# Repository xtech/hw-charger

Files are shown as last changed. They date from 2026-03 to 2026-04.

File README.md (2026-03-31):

# Universal OpenMower Charger

## Information

This hardware version is in beta state. Expect for things to not work at the current state!

## About This Repo

OpenMower is an open-source project that upgrades off-the-shelf robotic mowers into modern, smart lawn mowing robots with RTK GPS technology. For more details, check out the [OpenMower project](https://github.com/clemensElflein/openmower).

This repository contains the design files for a custom charger specifically designed for converting YardForce mowers to OpenMower. 

## Patents, Local Laws, Liability

Before building a robot based on the designs published here, please make sure that you are allowed to do so in your specific regions.
There may be patents and / or laws prohibiting you of doing so.

The code/schematics/PCB files are distributed in the hope that it will be useful, but WITHOUT ANY WARRANTY; without even the implied warranty of MERCHANTABILITY or FITNESS FOR A PARTICULAR PURPOSE.

This basically means: I'm just documenting a project of mine here for free and I don't have the time and resources to check that devices built using this information will be safe to use, legal to use or even work as intended. You will need technical know-how to use this project and I'm not liable for any damages your devices do to anyone or anything.

## License

<br />This work is licensed under a <a rel="license" href="https://creativecommons.org/licenses/by-nc/4.0/">Creative Commons Attribution-NonCommercial 4.0 International License</a>.

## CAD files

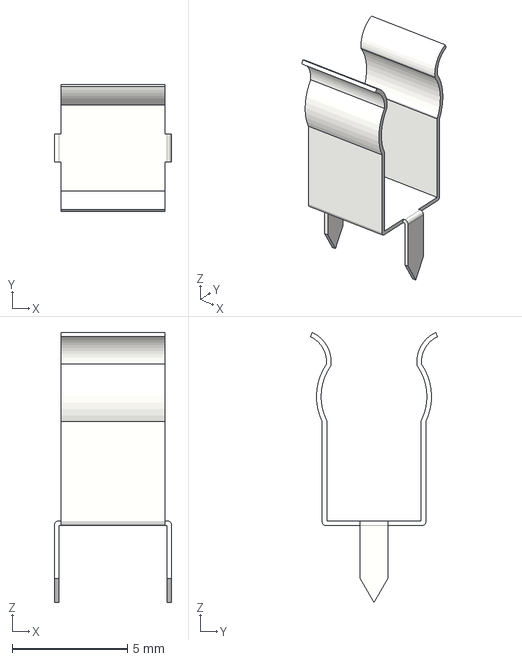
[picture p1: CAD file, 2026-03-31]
3d/FuseClip.stp
5.10 x 5.53 x 11.7 mm

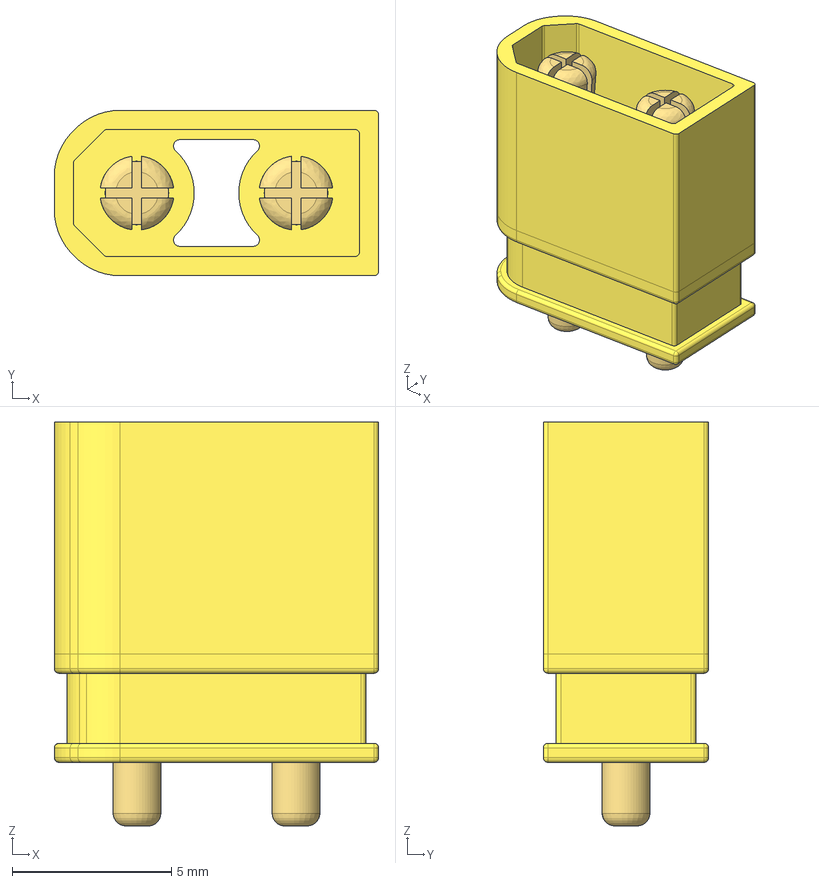
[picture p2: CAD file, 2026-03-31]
components/extern/3dmodels/easyeda2kicad/Amass_XT30UPB-M.step
10.2 x 5.20 x 12.7 mm

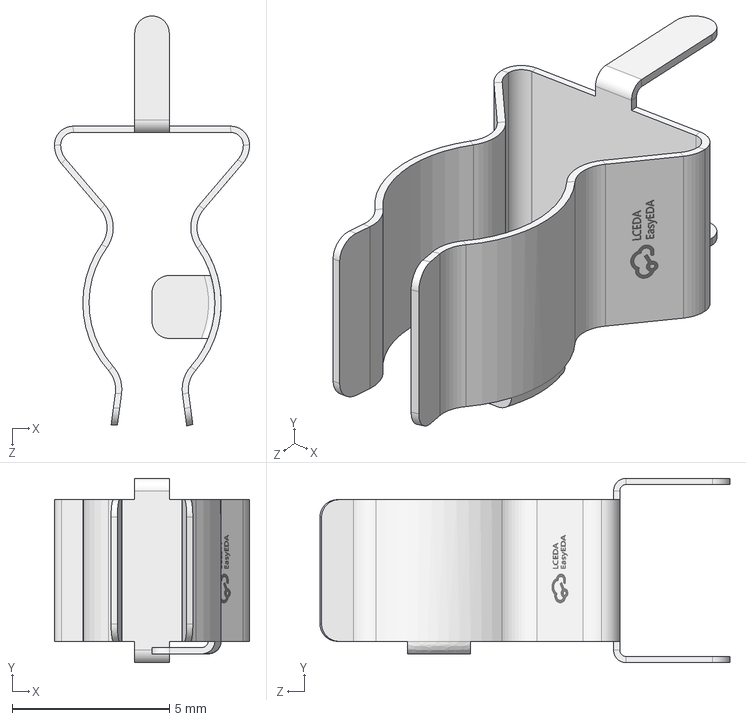
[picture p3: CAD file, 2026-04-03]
components/extern/3dmodels/local_FUSE/FUSE-TH_5X20.step
6.20 x 5.86 x 13.0 mm

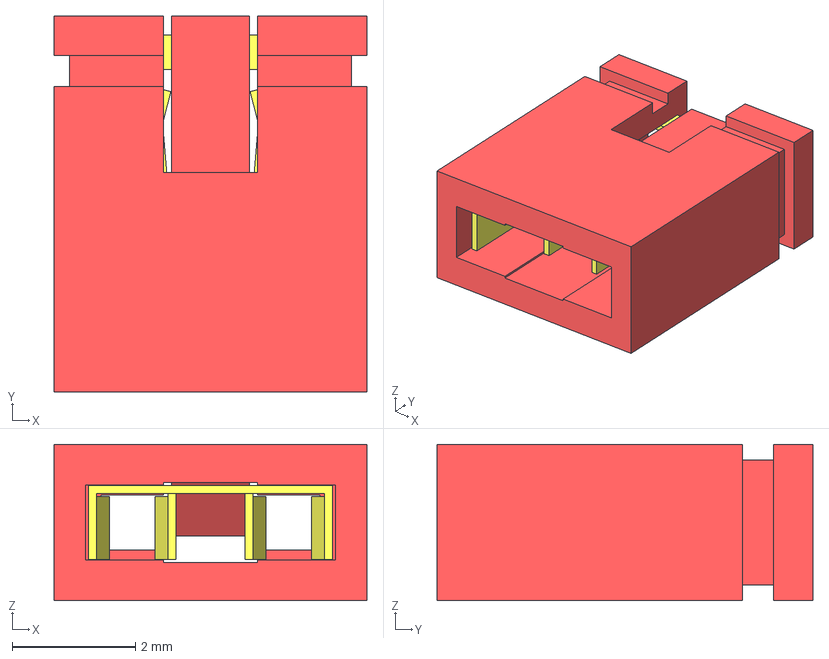
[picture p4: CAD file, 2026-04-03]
components/extern/3dmodels/SNT-100-RD-G.step
5.08 x 6.10 x 2.54 mm

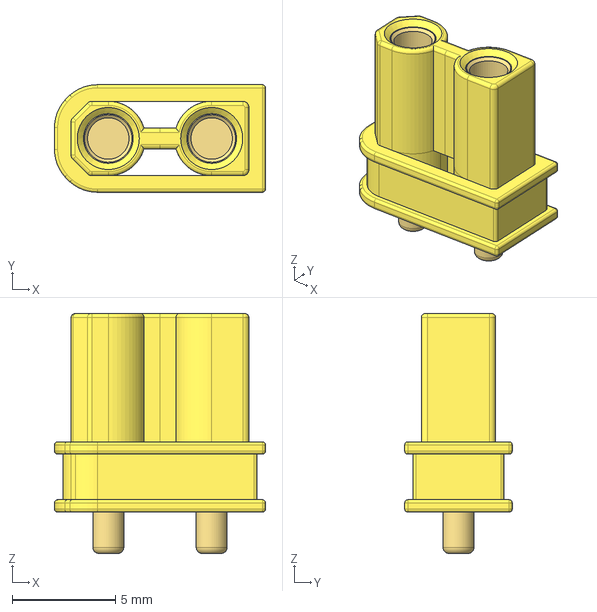
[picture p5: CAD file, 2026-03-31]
components/extern/3dmodels/easyeda2kicad/Amass_XT30UPB-F.step
10.2 x 5.20 x 11.6 mm

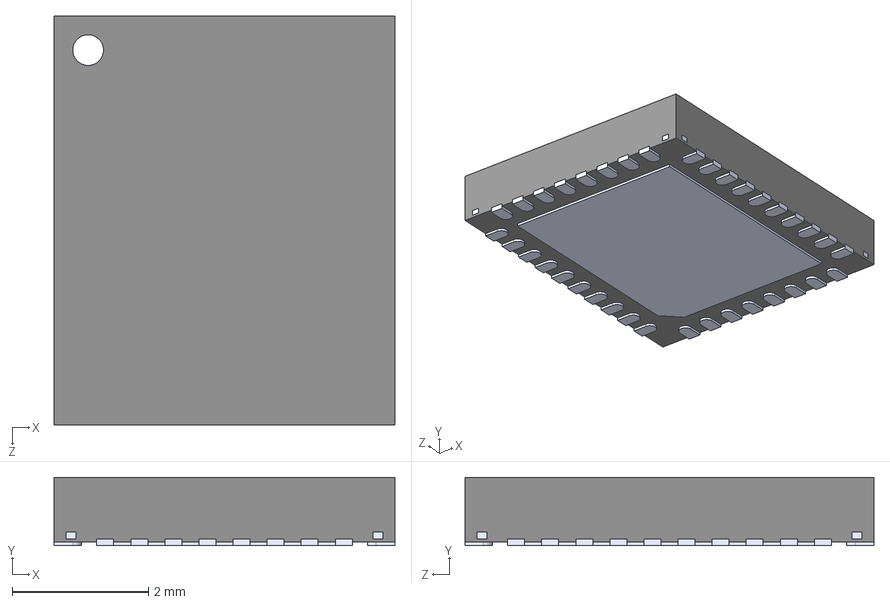
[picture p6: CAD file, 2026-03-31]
components/extern/3dmodels/local_CHARGER/BQ25756RRVR.step
5.00 x 1.00 x 6.00 mm

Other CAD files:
components/extern/3dmodels/SNT-100-BK-H.step
components/extern/3dmodels/SNT-100-BL-G.step

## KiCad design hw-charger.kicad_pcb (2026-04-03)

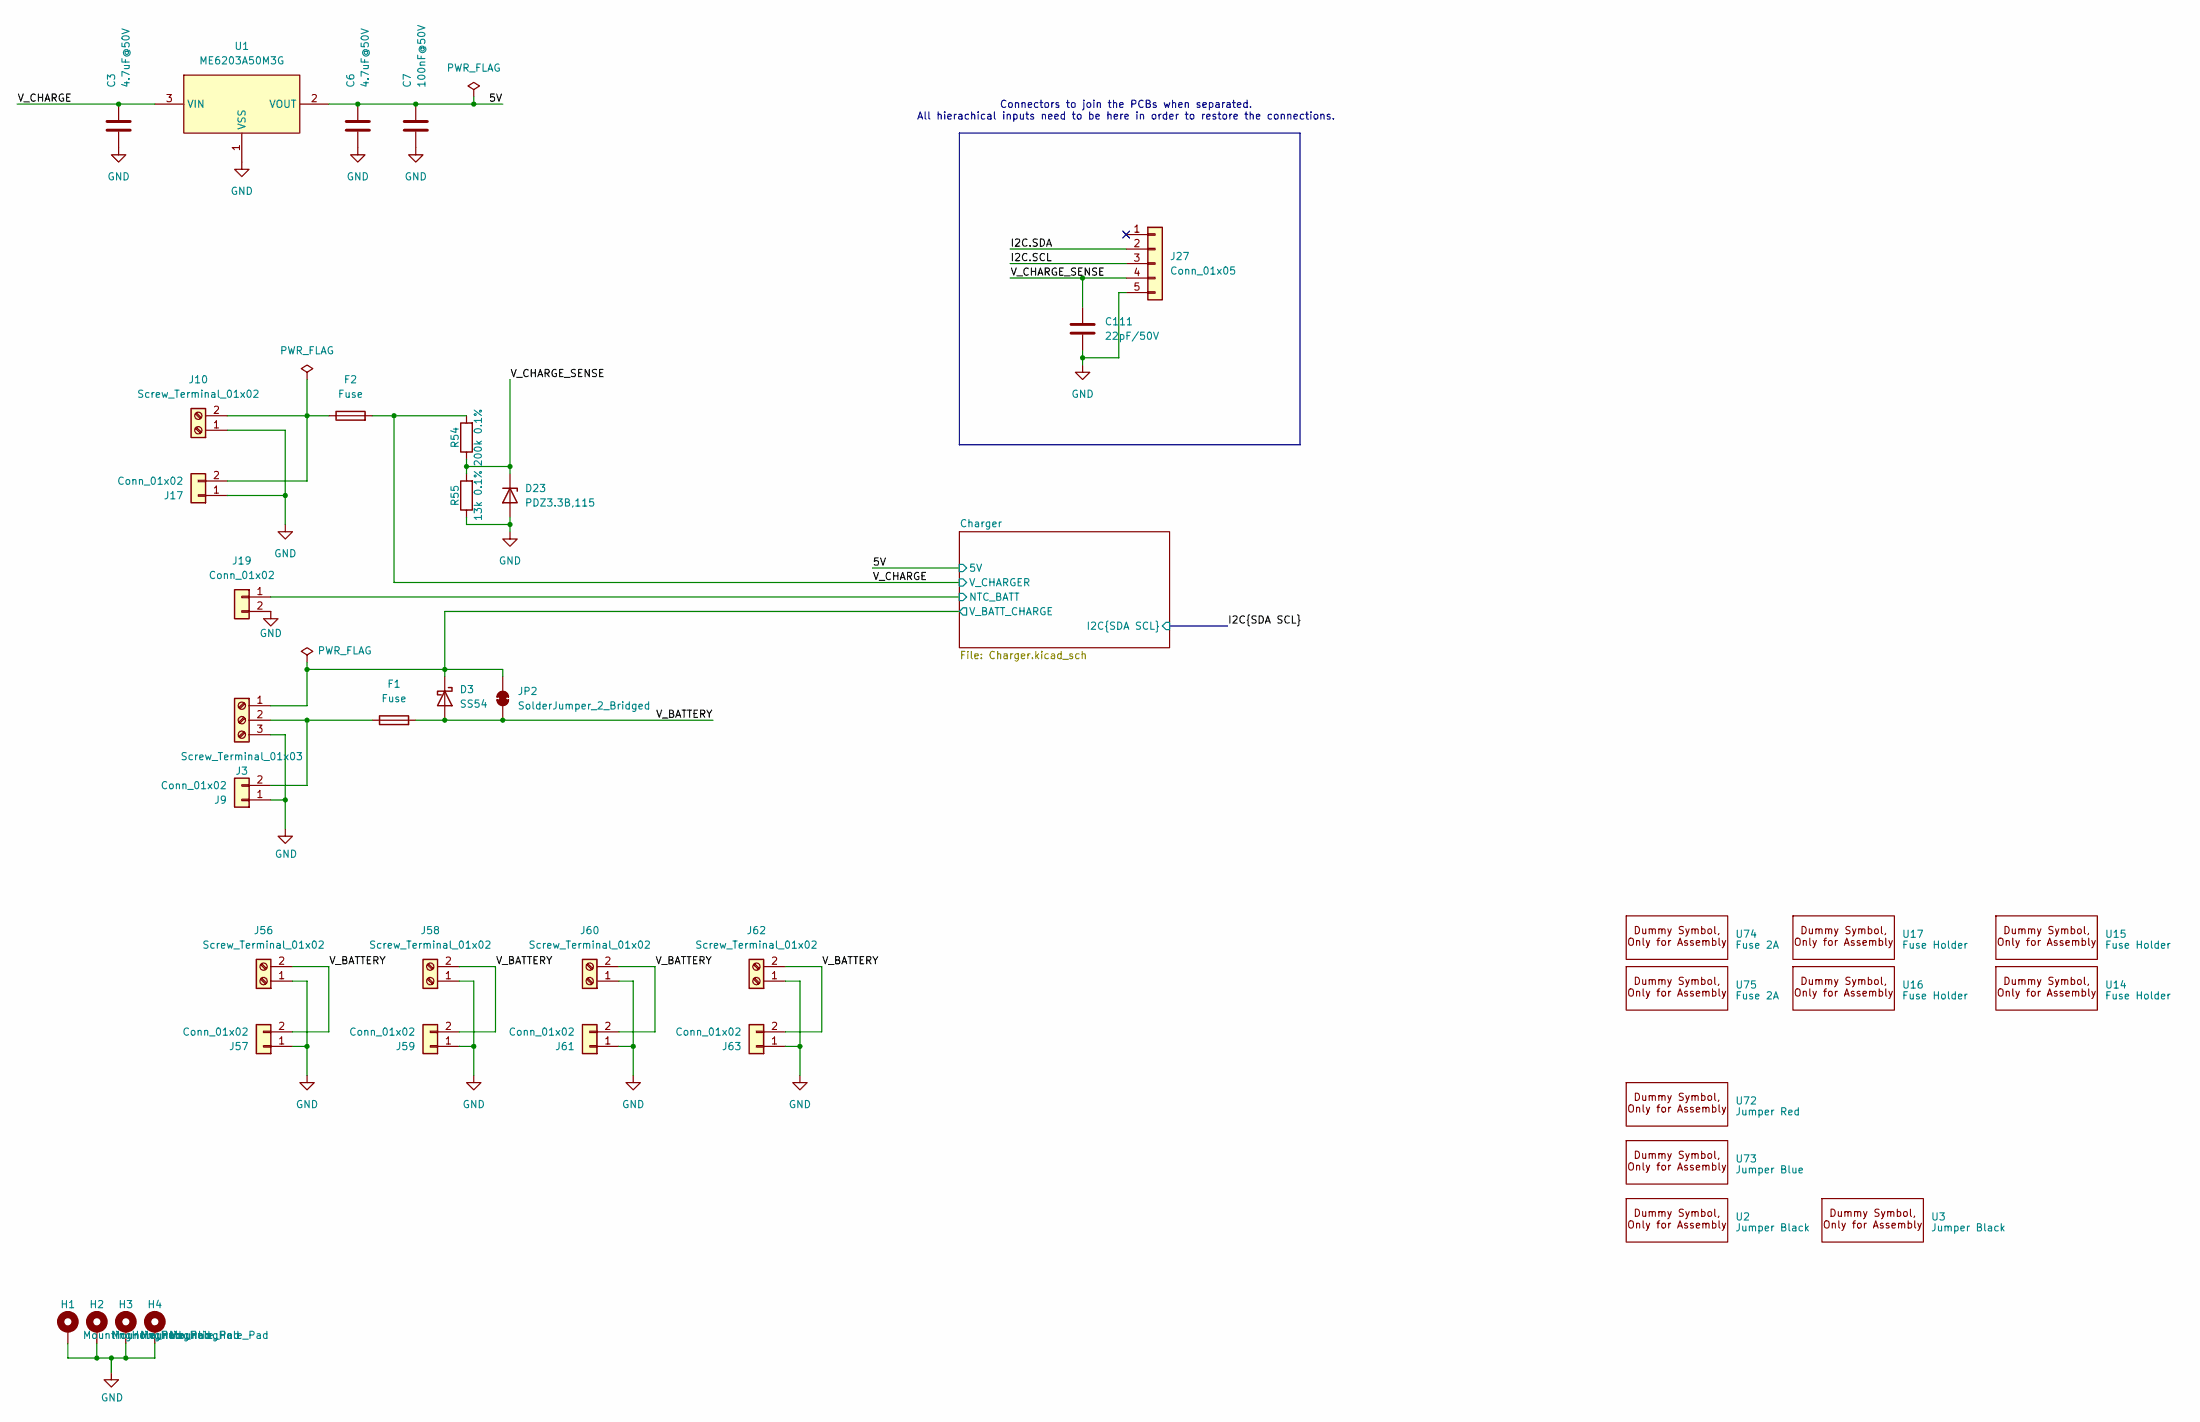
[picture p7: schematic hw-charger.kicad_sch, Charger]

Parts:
C3, C6: 4.7uF@50V; C_1206_3216Metric; JLC C29823
C7: 100nF@50V; C_0603_1608Metric; JLC C14663
C111: 22pF/50V; C_0603_1608Metric; JLC C1653
D3: SS54; D_SMA; Part Number SB54AFC_R1_00001; Digikey 3757-SB54AFC_R1_00001CT-ND
D23: PDZ3.3B,115; D_SOD-323; JLC C426855
F1, F2: Fuse; Fuseholder5x20_horiz_open_inline_C3130; JLC C3130
H1, H2, H3, H4: MountingHole_Pad; MountingHole_4.3mm_M4_Pad_Via
J3: Screw_Terminal_01x03; TerminalBlock_Phoenix_MKDS-1,5-3-5.08_1x03_P5.08mm_Horizont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; JLC C557666
J9, J17: Conn_01x02; AMASS_XT30U-M_1x02_P5.0mm_Vertical_mod; JLC C99101
J10, J56, J58, J60, J62: Screw_Terminal_01x02; TerminalBlock_Phoenix_MKDS-1,5-2-5.08_1x02_P5.08mm_Horizont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; JLC C557665
J19: Conn_01x02; JST_XH_B2B-XH-A_1x02_P2.50mm_Vertical; JLC C2910525
J27: Conn_01x05; JST_XH_B5B-XH-A_1x05_P2.50mm_Vertical; JLC C157991
J57, J59, J61, J63: Conn_01x02; AMASS_XT30U-F_1x02_P5.0mm_Vertical_mod; JLC C99102
JP2: SolderJumper_2_Bridged; SolderJumper-2_P1.3mm_Bridged2Bar_Pad1.0x1.5mm
R54: 200k 0.1%; R_0402_1005Metric; JLC C728556
R55: 13k 0.1%; R_0402_1005Metric; JLC C852524
U1: ME6203A50M3G; SOT-23-3_L2.9-W1.6-P1.90-LS2.8-BR; LCSC Part C92717
U2, U3: Jumper Black; SNT-100-BK-H; JLC C100114
U14, U15, U16, U17: Fuse Holder; Dummy; JLC C3130
U72: Jumper Red; SNT-100-RD-G; JLC C20417889
U73: Jumper Blue; SNT-100-BL-H; JLC C20417886
U74, U75: Fuse 2A; Dummy; JLC C356459

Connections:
/5V: C6.1, C7.2, U1.2 (VOUT); also elsewhere on the board
/Charger/NTC_BATT: J19.1; also elsewhere on the board
/Charger/V_BATT_CHARGE: D3.1 (K), J3.1, JP2.2 (B); also elsewhere on the board
/I2C.SCL: J27.3; also elsewhere on the board
/I2C.SDA: J27.2; also elsewhere on the board
/V_BATTERY: D3.2 (A), F1.2, J56.2, J57.2, J58.2, J59.2, J60.2, J61.2, J62.2, J63.2, JP2.1 (A)
/V_CHARGE: C3.1, F2.2, R54.2, U1.3 (VIN); also elsewhere on the board
/V_CHARGE_SENSE: C111.1, D23.1 (K), J27.4, R54.1, R55.2
GND: C3.2, C6.2, C7.1, C111.2, D23.2 (A), H1.1, H2.1, H3.1, H4.1, J3.3, J9.1, J10.1, J17.1, J19.2, J27.5, J56.1, J57.1, J58.1, J59.1, J60.1, J61.1, J62.1, J63.1, R55.1, U1.1 (VSS); also elsewhere on the board
unnamed: F1.1, J3.2, J9.2
unnamed: F2.1, J10.2, J17.2

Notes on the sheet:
Connectors to join the PCBs when separated. All hierachical inputs need to be here in order to restore the connections.

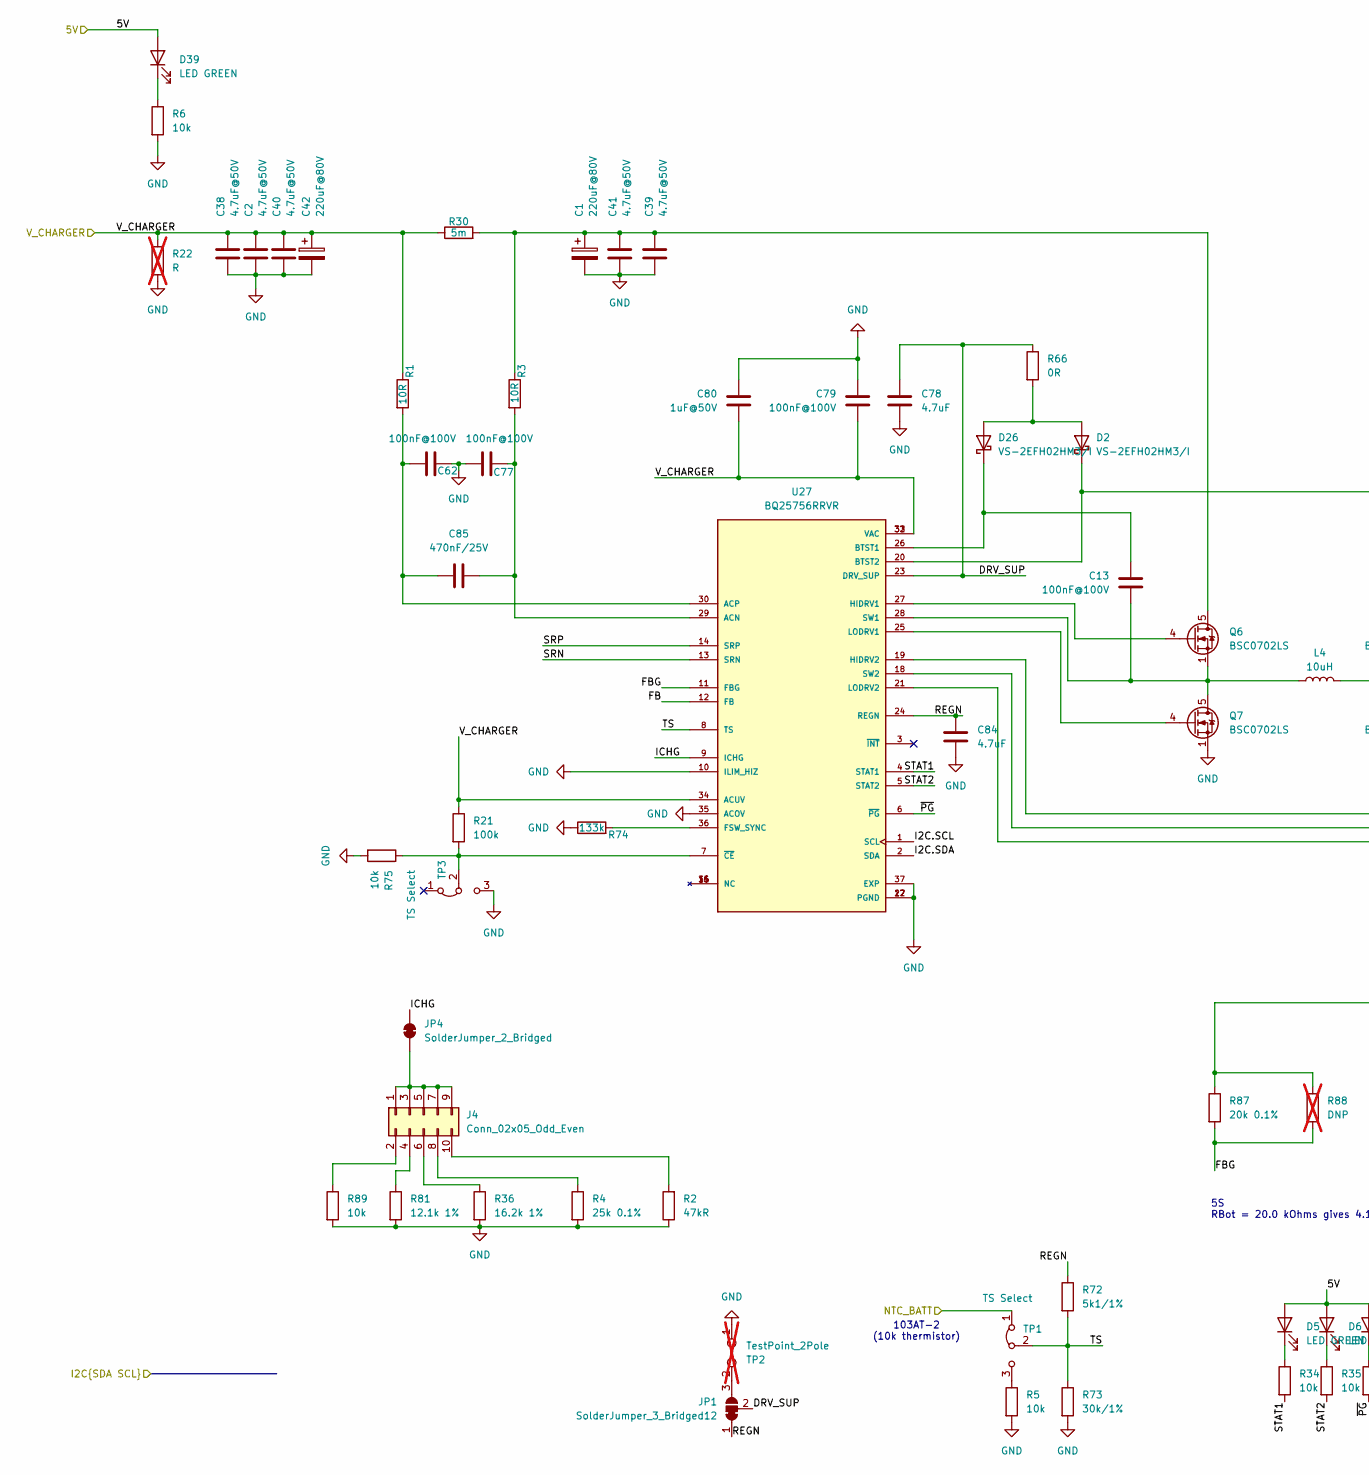
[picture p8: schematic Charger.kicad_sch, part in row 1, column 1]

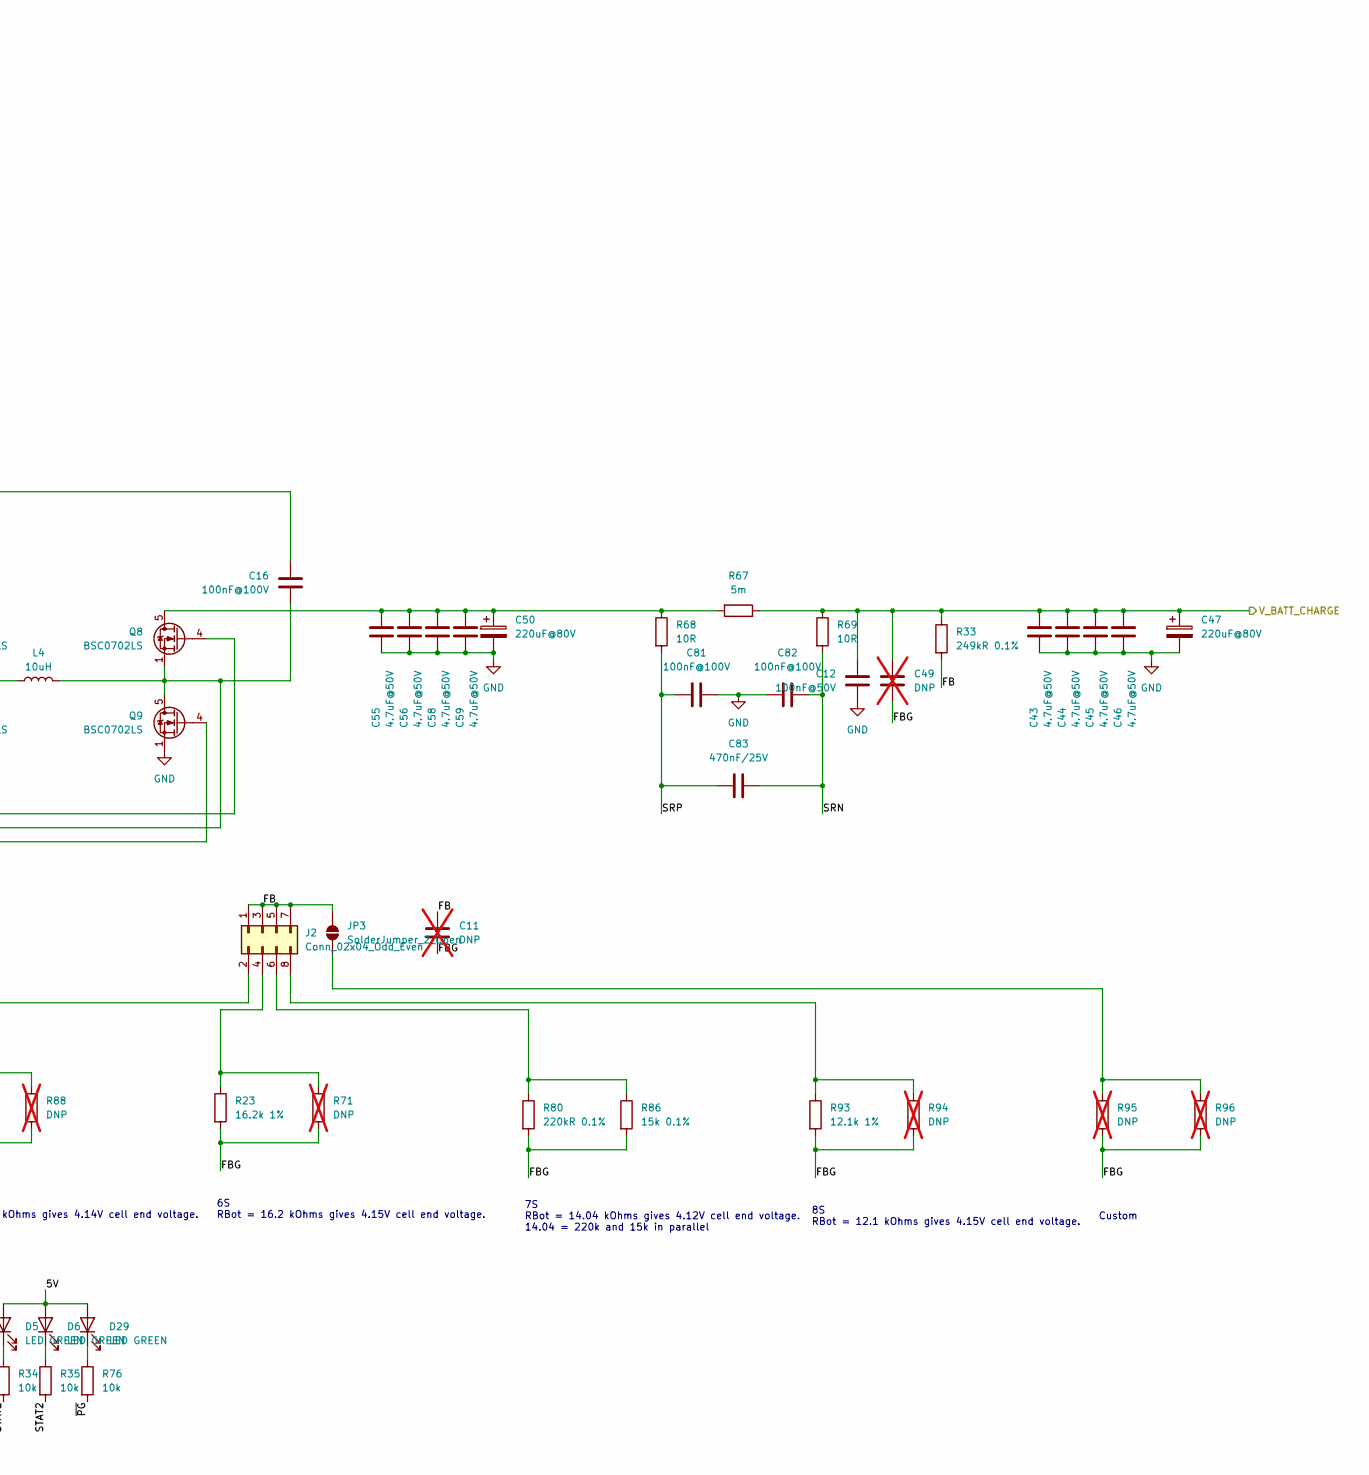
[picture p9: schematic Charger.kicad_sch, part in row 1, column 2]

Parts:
C1, C42, C47, C50: 220uF@80V; CP_Radial_D10.0mm_P5.00mm; JLC C2937593
C2, C38, C39, C40, C41, C43, C44, C45, C46, C55, C56, C58, C59: 4.7uF@50V; C_1206_3216Metric; JLC C29823
C11, C49: DNP; C_0603_1608Metric; not fitted
C12: 100nF@50V; C_0603_1608Metric; JLC C14663
C13, C16, C62, C77, C79, C81, C82: 100nF@100V; C_0805_2012Metric; JLC C28233
C78, C84: 4.7uF; C_0805_2012Metric; JLC C1779
C80: 1uF@50V; C_0805_2012Metric; JLC C28323
C83, C85: 470nF/25V; C_0603_1608Metric; JLC C1623
D2, D26: VS-2EFH02HM3/I; D_SMF; JLC C241868
D5, D6, D29, D39: LED GREEN; LED_0805_2012Metric; JLC C2297
J2: Conn_02x04_Odd_Even; PinHeader_2x04_P2.54mm_Vertical; JLC C5383105
J4: Conn_02x05_Odd_Even; PinHeader_2x05_P2.54mm_Vertical; JLC C706895
JP1: SolderJumper_3_Bridged12; SolderJumper-3_P1.3mm_Bridged12_Pad1.0x1.5mm
JP3: SolderJumper_2_Open; SolderJumper-2_P1.3mm_Open_Pad1.0x1.5mm
JP4: SolderJumper_2_Bridged; SolderJumper-2_P1.3mm_Bridged_Pad1.0x1.5mm
L4: 10uH; L_Sunlord_MWSA1004S; JLC C408487
Q6, Q7, Q8, Q9: BSC0702LS; TDSON-8-1; JLC C501503
R1, R3, R68, R69: 10R; R_0603_1608Metric; JLC C22859
R2: 47kR; R_0603_1608Metric; JLC C25819
R4: 25k 0.1%; R_0603_1608Metric; JLC C2828637
R5, R6, R34, R35, R75, R76: 10k; R_0402_1005Metric; JLC C25744
R21: 100k; R_0402_1005Metric; JLC C25741
R22: R; R_1206_3216Metric; not fitted
R23, R36: 16.2k 1%; R_0603_1608Metric; JLC C22885
R30, R67: 5m; R_2512_6332Metric; JLC C185817
R33: 249kR 0.1%; R_0603_1608Metric; JLC C705752
R66: 0R; R_0805_2012Metric; JLC C17477
R71, R88, R94, R95, R96: DNP; R_0603_1608Metric; not fitted
R72: 5k1/1%; R_0603_1608Metric; JLC C23186
R73: 30k/1%; R_0603_1608Metric; JLC C22984
R74: 133k; R_0603_1608Metric; JLC C227577
R80: 220kR 0.1%; R_0603_1608Metric; JLC C278545
R81, R93: 12.1k 1%; R_0603_1608Metric; JLC C22864
R86: 15k 0.1%; R_0603_1608Metric; JLC C2692707
R87: 20k 0.1%; R_0603_1608Metric; JLC C4184
R89: 10k; R_0603_1608Metric; JLC C25804
TP1, TP3: TS Select; PinHeader_1x03_P2.54mm_Vertical; JLC C49257
TP2: TestPoint_2Pole; PinHeader_1x02_P2.54mm_Vertical; not fitted
U27: BQ25756RRVR; PARTREV August 2023; JLC C19272232

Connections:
/5V: D5.2 (A), D6.2 (A), D29.2 (A), D39.2 (A); also elsewhere on the board
/Charger/DRV_SUP: C78.1, JP1.2 (C), R66.1, U27.23 (DRV_SUP)
/Charger/FB: C11.1, J2.1, J2.3, J2.5, J2.7, JP3.2 (B), R33.2, U27.12 (FB)
/Charger/FBG: C11.2, C49.2, R23.2, R71.2, R80.2, R86.2, R87.2, R88.2, R93.2, R94.2, R95.2, R96.2, U27.11 (FBG)
/Charger/ICHG: JP4.2 (B), U27.9 (ICHG)
/Charger/NTC_BATT: TP1.1 (A); also elsewhere on the board
/Charger/REGN: C84.1, JP1.1 (A), R72.1, U27.24 (REGN)
/Charger/SRN: C82.1, C83.2, R69.2, U27.13 (SRN)
/Charger/SRP: C81.2, C83.1, R68.2, U27.14 (SRP)
/Charger/STAT1: R34.2, U27.4 (STAT1)
/Charger/STAT2: R35.2, U27.5 (STAT2)
/Charger/TS: R72.2, R73.1, TP1.2 (C), U27.8 (TS)
/Charger/V_BATT_CHARGE: C12.2, C43.1, C44.1, C45.1, C46.1, C47.1, C49.1, R33.1, R67.1, R69.1; also elsewhere on the board
/Charger/~PG: R76.2, U27.6 (~PG)
/I2C.SCL: U27.1 (SCL); also elsewhere on the board
/I2C.SDA: U27.2 (SDA); also elsewhere on the board
/V_CHARGE: C2.1, C38.1, C40.1, C42.1, C79.1, C80.1, R1.1, R21.1, R22.1, R30.1, U27.32 (VAC), U27.33 (VAC), U27.34 (ACUV); also elsewhere on the board
GND: C1.2, C2.2, C12.1, C38.2, C39.2, C40.2, C41.2, C42.2, C43.2, C44.2, C45.2, C46.2, C47.2, C50.2, C55.2, C56.2, C58.2, C59.2, C62.2, C77.1, C78.2, C79.2, C80.2, C81.1, C82.2, C84.2, Q7.1 (S), Q7.2 (S), Q7.3 (S), Q9.1 (S), Q9.2 (S), Q9.3 (S), R2.1, R4.2, R5.2, R6.2, R22.2, R36.2, R73.2, R74.1, R75.2, R81.2, R89.2, TP2.1, TP3.3 (B), U27.10 (ILIM_HIZ), U27.17 (PGND), U27.22 (PGND), U27.35 (ACOV), U27.37 (EXP); also elsewhere on the board
unnamed: D2.2 (A), D26.2 (A), R66.2
unnamed: C16.2, D2.1 (K), U27.20 (BTST2)
unnamed: D5.1 (K), R34.1
unnamed: D6.1 (K), R35.1
unnamed: C13.2, D26.1 (K), U27.26 (BTST1)
unnamed: D29.1 (K), R76.1
unnamed: D39.1 (K), R6.1
unnamed: J2.2, R87.1, R88.1
unnamed: J2.4, R23.1, R71.1
unnamed: J2.6, R80.1, R86.1
unnamed: J2.8, R93.1, R94.1
unnamed: J4.1, J4.3, J4.5, J4.7, J4.9, JP4.1 (A)
unnamed: J4.2, R89.1
unnamed: J4.4, R81.1
unnamed: J4.6, R36.1
unnamed: J4.8, R4.1
unnamed: J4.10, R2.2
unnamed: JP1.3 (B), TP2.2
unnamed: JP3.1 (A), R95.1, R96.1
unnamed: C1.1, C39.1, C41.1, Q6.5 (D), R3.1, R30.2
unnamed: Q6.4 (G), U27.27 (HIDRV1)
unnamed: C13.1, L4.1, Q6.1 (S), Q6.2 (S), Q6.3 (S), Q7.5 (D), U27.28 (SW1)
unnamed: Q7.4 (G), U27.25 (LODRV1)
unnamed: C50.1, C55.1, C56.1, C58.1, C59.1, Q8.5 (D), R67.2, R68.1
unnamed: Q8.4 (G), U27.19 (HIDRV2)
unnamed: C16.1, L4.2, Q8.1 (S), Q8.2 (S), Q8.3 (S), Q9.5 (D), U27.18 (SW2)
unnamed: Q9.4 (G), U27.21 (LODRV2)
unnamed: R5.1, TP1.3 (B)
unnamed: R21.2, R75.1, TP3.2 (C), U27.7 (~CE)
unnamed: C77.2, C85.1, R3.2, U27.29 (ACN)
unnamed: C62.1, C85.2, R1.2, U27.30 (ACP)
unnamed: R74.2, U27.36 (FSW_SYNC)

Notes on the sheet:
6S RBot = 16.2 kOhms gives 4.15V cell end voltage.
103AT-2 (10k thermistor)
Custom
7S RBot = 14.04 kOhms gives 4.12V cell end voltage. 14.04 = 220k and 15k in parallel
5S RBot = 20.0 kOhms gives 4.14V cell end voltage.
8S RBot = 12.1 kOhms gives 4.15V cell end voltage.

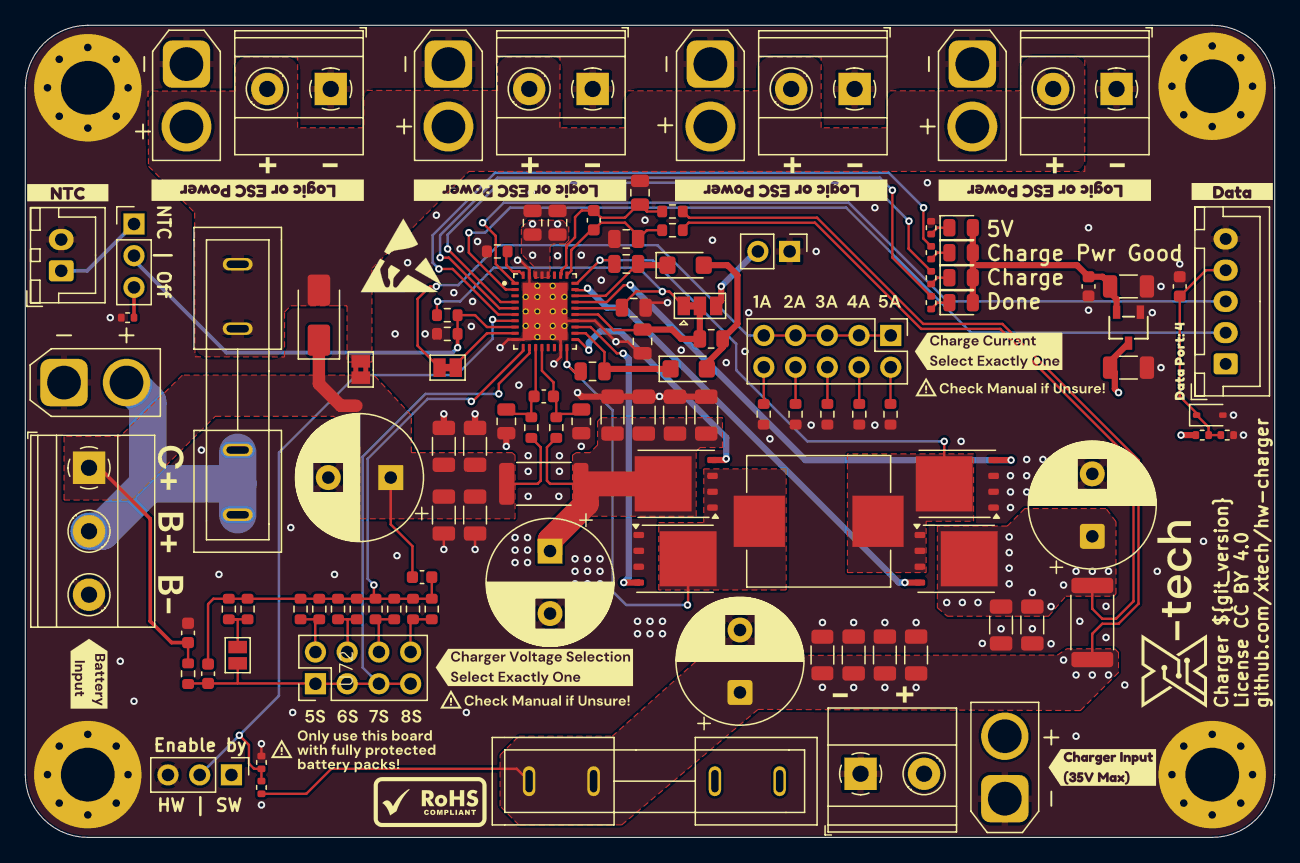
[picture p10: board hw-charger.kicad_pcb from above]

Board: 4 copper layers, 100.0 x 65.0 mm, 163 parts (0 on the bottom side), 54 nets.

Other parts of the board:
LOGO2: ESD-Logo_6.6x6mm_SilkScreen
kibuzzard-69C99438, kibuzzard-69C99438#2, kibuzzard-69C99438#3: G***; kibuzzard-69C99438
kibuzzard-69C99648: G***; kibuzzard-69C99648
kibuzzard-69CD6E52: G***; kibuzzard-69CD6E52
kibuzzard-69CEE1A3: G***; kibuzzard-69CEE1A3
kibuzzard-69CEE455: G***; kibuzzard-69CEE455
kibuzzard-69CEEB52: G***; kibuzzard-69CEEB52
kibuzzard-69CFD05E: G***; kibuzzard-69CFD05E
kibuzzard-69CFD081: G***; kibuzzard-69CFD081
kibuzzard-670E8F90: G***; kibuzzard-670E8F90
kibuzzard-670E90ED, kibuzzard-670E90ED#2: G***; kibuzzard-670E90ED
kibuzzard-670E91C7: G***; kibuzzard-670E91C7
kibuzzard-670E91D3: G***; kibuzzard-670E91D3
kibuzzard-670E91D8: G***; kibuzzard-670E91D8
kibuzzard-670E91E3: G***; kibuzzard-670E91E3
kibuzzard-6711AB8A: G***; kibuzzard-6711AB8A
kibuzzard-68532E1B, kibuzzard-68532E1B#2, kibuzzard-68532E1B#3, kibuzzard-68532E1B#4, kibuzzard-68532E1B#5: G***; kibuzzard-68532E1B
kibuzzard-68532E12, kibuzzard-68532E12#2, kibuzzard-68532E12#3, kibuzzard-68532E12#4, kibuzzard-68532E12#5: G***; kibuzzard-68532E12
kibuzzard-671188B5: G***; kibuzzard-671188B5
kibuzzard-671188C2: G***; kibuzzard-671188C2
kibuzzard-671188D3: G***; kibuzzard-671188D3
kibuzzard-671188DE: G***; kibuzzard-671188DE
kibuzzard-671188EA: G***; kibuzzard-671188EA
kibuzzard-67111882: G***; kibuzzard-67111882
kibuzzard-67111937: G***; kibuzzard-67111937
kibuzzard-67111945: G***; kibuzzard-67111945

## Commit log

2026-03-31 Add FT rotations and kibot filter and set fuses DNP
    [Charger.kicad_sch, hw-charger.kicad_pcb, hw-charger.kicad_sch]
2026-04-01 Add AC-Sense
    [Charger.kicad_sch, hw-charger.kicad_pcb]
2026-04-03 Add /CE, NTC Selector, 5V LDO. Fix copper traces, vias in pads and this and that
    [Charger.kicad_sch, FUSE-TH_5X20.step, SNT-100-BK-H.step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]
2026-04-03 Fixed CE pin connection; Use git version as variable
    [Charger.kicad_sch, hw-charger.kicad_pcb]

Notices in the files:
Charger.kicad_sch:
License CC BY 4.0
